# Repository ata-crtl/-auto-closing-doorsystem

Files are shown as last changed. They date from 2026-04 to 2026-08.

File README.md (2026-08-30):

# Automatic Door Closer

This is a rechargible door closer, it is designed to comabt the issue of people always leaveing my door open.You push the button once and there you go , the motor pulls in the fishing wire meaning you now have the ability to close the door from your bed. 

This system has a seprate remote and employs to esp32s to comunicate amongst each other and close the door from your bed. It is also desighned to be rechargible so you can maintain it.

## Features

- Rechargeable power system.
- ESP32 based control system.
- Separate remote Control
- Made to mount onto a door and above the door frame.

## Important Safety Check

Before attaching the wires to the ESP32 VIN pin, use a multimeter to make sure the wire coming from the buck converter is **5V** to not fry your esp and the same for the remote power output before connecting it to the ESP32.

## CAD

**Onshape link:**  
[View the Onshape model](https://cad.onshape.com/documents/bdd11de85f4570d51cb36bd7/w/b7536c01ad29c059d531be40/e/07df8b484f8b3f7ee84a2b9b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)

## Main Build Preview



## Bill of Materials

| Item | Notes | Link |
|---|---|---|
| ESP32 | Main controller for the door closer | https://www.aliexpress.com/item/1005008981904299.html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 |
| ESP32 | Controller used in the sender remote | https://www.aliexpress.com/item/1005008981904299.html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 |
| L298N motor driver | Drives the main motor | https://www.aliexpress.com/item/1005006794464360.html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 |
| High-power motor | Provides the force to close the door | https://www.aliexpress.com/item/1005008531655044.html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 |
| USB-C charging module | Charges the battery in the main unit | https://www.aliexpress.com/item/1005009041347980.html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 |
| TP4056 charging module | Charges the battery in the remote | https://www.aliexpress.com/item/1005012026232715.html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 |
| Buck converter | Steps voltage down to 5V for the ESP32 | https://www.aliexpress.com/item/1005011787585923.html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 |
| Boost/step-up module | Steps voltage up for the remote ESP32 | https://www.aliexpress.com/item/1005008964880397.html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 |
| Rechargeable battery | Main power source (12V) | https://www.aliexpress.com/item/32991156265.html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 |
| Rechargeable battery | Remote power source (3.7V) | https://www.aliexpress.com/item/1005008217717191.html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 |
| Push button | Used to trigger the system | https://www.aliexpress.com/item/1005007604615720.html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 |
| Fishing line | Connects the pulley system to the door | https://www.aliexpress.com/item/1005003972138352.html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 |
| Screws | Used to mount the mechanism and close the case (8mm) | https://www.aliexpress.com/item/1005003986879500.html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 |
| Screws | Used to mount the mechanism and close the case (20mm) | https://www.aliexpress.com/item/1005008669605569.html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 |
| Threaded inserts | Brass heat-set inserts for housing assembly | https://www.aliexpress.com/item/1005008897571758.html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 |
| Adhesive for wood | Used where needed for secure mounting | N/A |
| Multimeter | Needed to verify output voltage before wiring | N/A |
## Main Unit Connections

| Part | Pin | Connects to |
|---|-----|---|
| USB-C charging module | VO+ | Battery red (+) |
| USB-C charging module | VO- | Battery black (-) |
| Battery | Red (+) | Buck converter IN+ |
| Battery | Black (-) | Buck converter IN- |
| Battery | Black (-) | L298N GND terminal |
| Battery | Black (-) | USB-C module VO- |
| Buck converter | OUT+ | ESP32 VIN or 5V |
| Buck converter | OUT- | ESP32 GND |
| Battery | Red (+) | L298N 12V |
| Battery | Black (-) | L298N GND terminal |
| ESP32 | GPIO 12 | L298N IN1 |
| ESP32 | GPIO 13 | L298N IN2 |

Main unit wiring diagram

## Sender Remote Connections

| Part | Pin | Connects to |
|---|-----|---|
| Button | Leg 1 | ESP32 GPIO 15 |
| Button | Leg 2 | ESP32 GND |
| Battery | Positive | TP4056 B+ |
| Battery | Negative | TP4056 B- |
| TP4056 | OUT+ | Boost module VIN+ |
| TP4056 | OUT- | Boost module VIN- |
| Step-up module | VOUT+ | ESP32 5V |
| Step-up module | VOUT- | ESP32 GND |

## Electronics Overview

Electronics overview

## Assembly Instructions

### Main Mechanism

**Step 1:** Connect all the electronics.

**Step 2:** Connect these parts as shown below.

Assembly step 2

**Step 3:** Insert the assembly into the main frame as shown.

Assembly step 3

**Step 4:** Insert the part shown into the pulley system, then attach the motor.

Assembly step 4

**Step 5:** Insert the heated threaded inserts in the locations shown below.

Threaded inserts 1

Threaded inserts 2

Threaded inserts 3

Threaded inserts 4

Threaded inserts 5

**Step 6:** Secure the motor using the inserts as shown.

Motor secured

**Step 7:** Use three screws to secure the lid.

Assembly step 5

**Step 8:** Secure the unit to the door using four 20 mm screws.

Assembly step 6

**Step 9:** Attach the top mount above the door using four screws.

Assembly step 7

**Step 10:** Tie one end of the fishing line to the hole in the pulley wheel and the other end to the hook above the door.

Assembly step 8

### Remote

**Step 1:** Put the button through the hole in the lid.

Remote step 1

**Step 2:** Attach the electronics.

**Step 3:** Close the lid and screw it down using four screws.

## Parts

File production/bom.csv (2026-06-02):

Item | amount | Price (£) | Link
Nylon Monofilament Fishing Line 0.20mm | 1 | 0.75 | https://www.aliexpress.com/item/1005003972138352.html?curPageLogUid=2XcZ4Ww9MPOc
planetry gear motor 12v 222rpm shaft diameter8mm | 1 | 10.8 | https://www.aliexpress.com/item/1005008531655044.html?curPageLogUid=7DNxVExLPLAy
esp32 wroom | 2 | 8 | https://www.aliexpress.com/item/1005008981904299.html?curPageLogUid=QJ0YR3t2WHge
L298N | 1 | 1.93 | https://www.aliexpress.com/item/1005006794464360.html?curPageLogUid=icuTPAe6avr6
12V '1200mh lion battery | 1 | 6.19 | https://www.aliexpress.com/item/32991156265.html?curPageLogUid=CGYJoRuEcVPL
LM2596S step down | 1 | 0.61 | https://www.aliexpress.com/item/1005011787585923.html?curPageLogUid=YjcrZrW1Brqj
LION CHARGER | 1 | 2.12 | https://www.aliexpress.com/item/1005009041347980.html?curPageLogUid=TGs7hIvKGiPt
M2.5 * 8 screws | 11 | 2.88 | https://www.aliexpress.com/item/1005003986879500.html
metal button 16mm | 1 | 1.52 | https://www.aliexpress.com/item/1005007604615720.html?curPageLogUid=HykUMbSzUJwT
M2.5 * 20 screws | 8 | 1.90 | https://www.aliexpress.com/item/1005008669605569.html?curPageLogUid=YJ37Ofc631Vz
tp4056 | 1 | 0.33 | https://www.aliexpress.com/item/1005012026232715.html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
lipo battery 3.7v | 1 | 8.15 | https://www.aliexpress.com/item/1005008217717191.html?curPageLogUid=0eatIcatYKIL
XL6019 voltage boost unit | 1 | 1.72 | https://www.aliexpress.com/item/1005008964880397.html?curPageLogUid=0kPCptXNzxTl
3.5mmOD-m2.5mm threaded insterts | 18 | 2 | https://www.aliexpress.com/item/1005008897571758.html?curPageLogUid=Z5a6lezLlS6j
TOTAL |  | 49

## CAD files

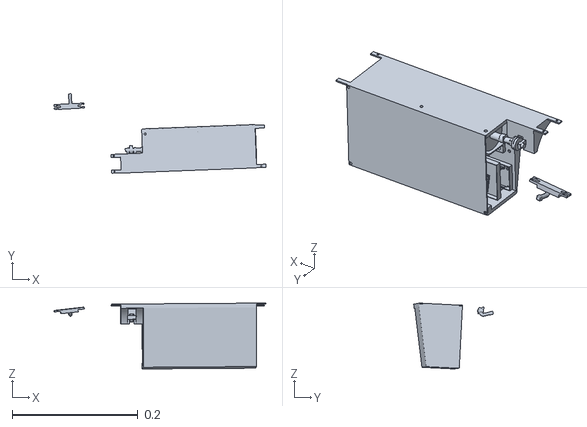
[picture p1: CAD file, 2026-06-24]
production/cad/Assembly 1 (2).stl
0.337 x 0.126 x 0.105

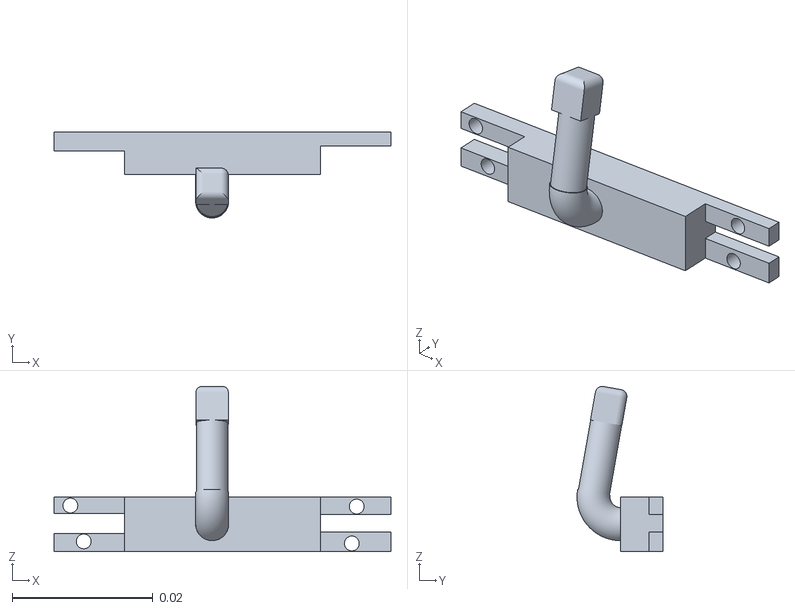
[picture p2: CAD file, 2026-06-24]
production/cad/Part Studio 3 (1).stl
0.0478 x 0.0122 x 0.0234

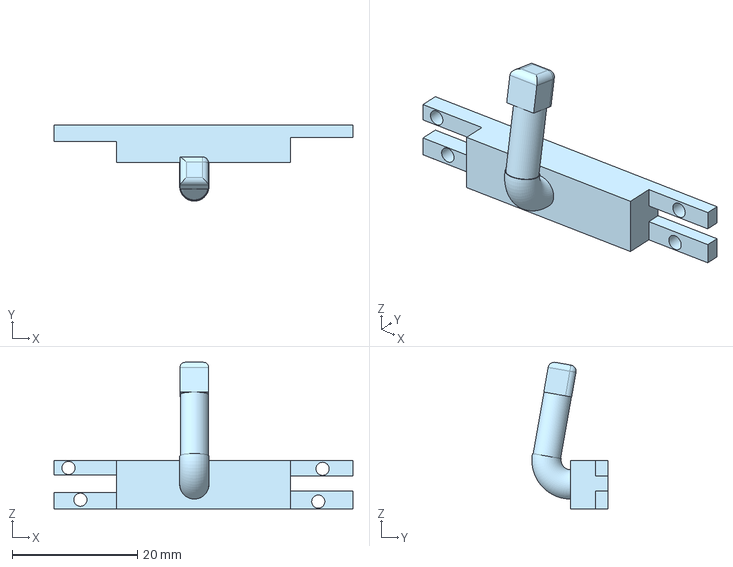
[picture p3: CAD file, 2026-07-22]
production/cad/stl cad files/Part Studio 3.step
47.8 x 12.2 x 23.4 mm

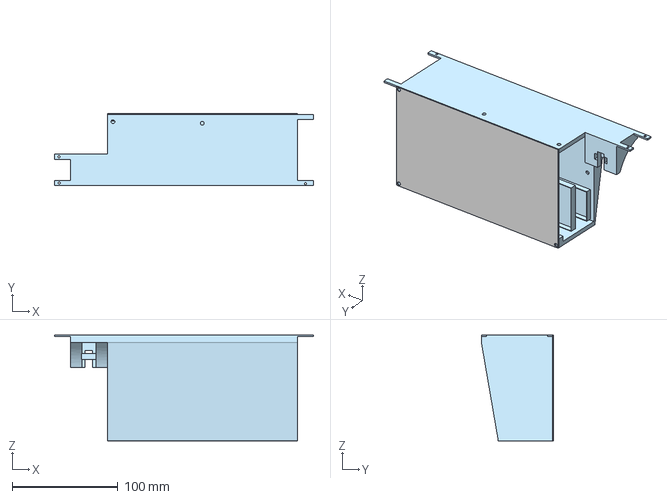
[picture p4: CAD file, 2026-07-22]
production/cad/stl cad files/frame.step
245.0 x 68.5 x 100.0 mm

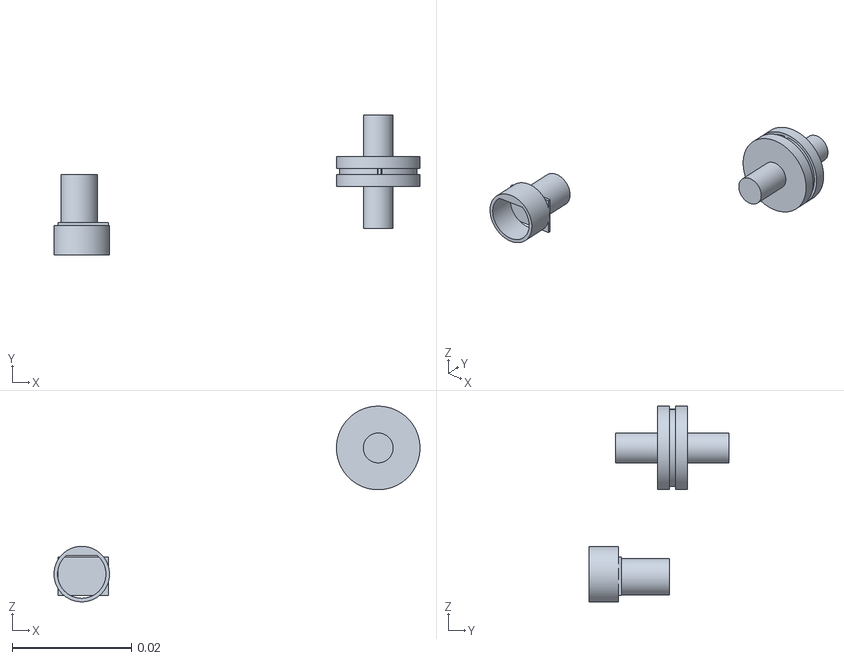
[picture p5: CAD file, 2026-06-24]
production/cad/Part Studio 2 (2).stl
0.0613 x 0.0235 x 0.0328

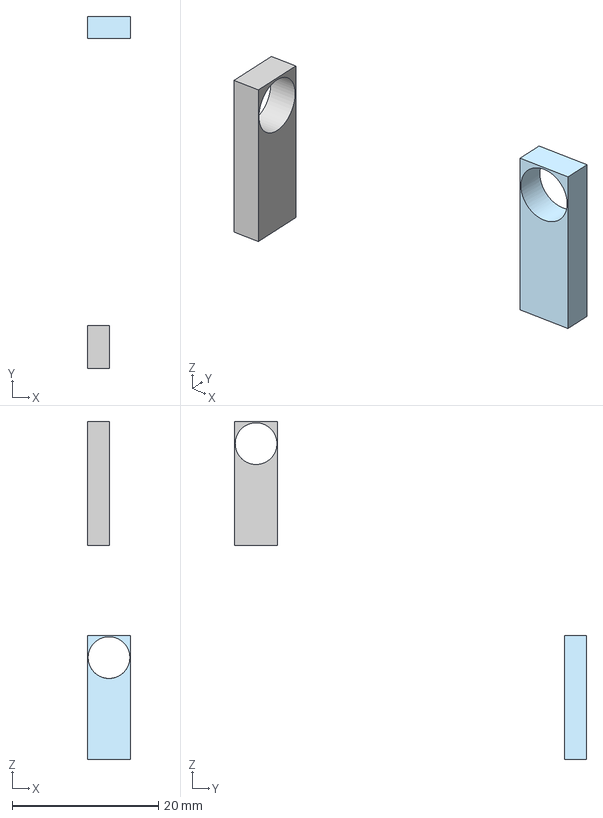
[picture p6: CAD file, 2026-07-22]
production/cad/stl cad files/Part Studio 4.step
5.90 x 48.1 x 46.2 mm

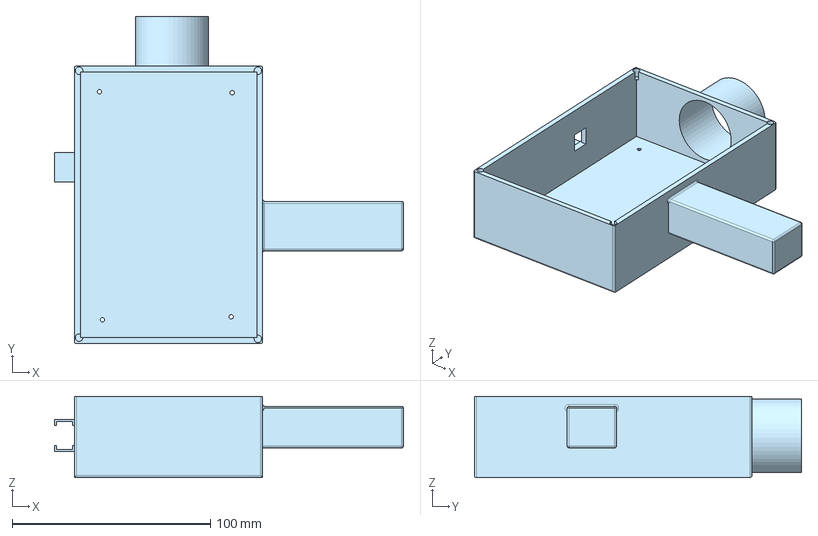
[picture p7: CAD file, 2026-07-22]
production/cad/stl cad files/Part Studio 1.step
176.0 x 165.0 x 41.0 mm

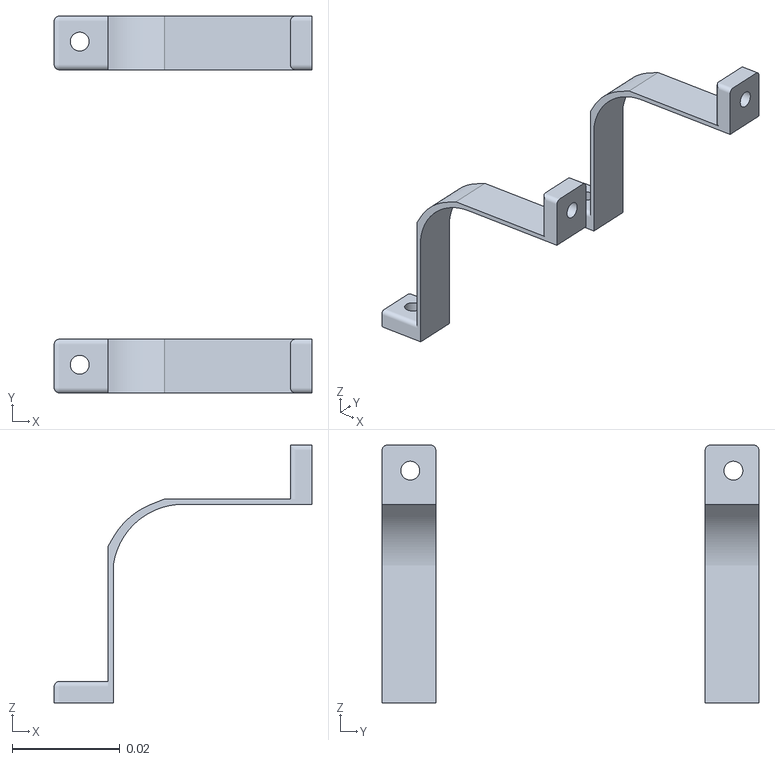
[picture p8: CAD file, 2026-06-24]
production/cad/holders motor.stl
0.0479 x 0.07 x 0.0479

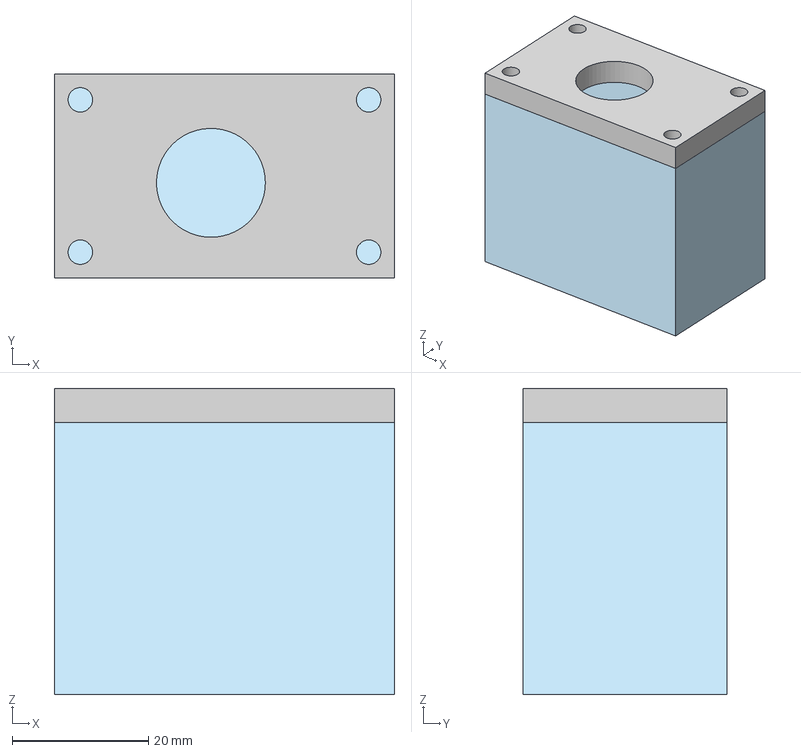
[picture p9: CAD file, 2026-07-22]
production/cad/stl cad files/remote.step
50.0 x 30.0 x 45.0 mm

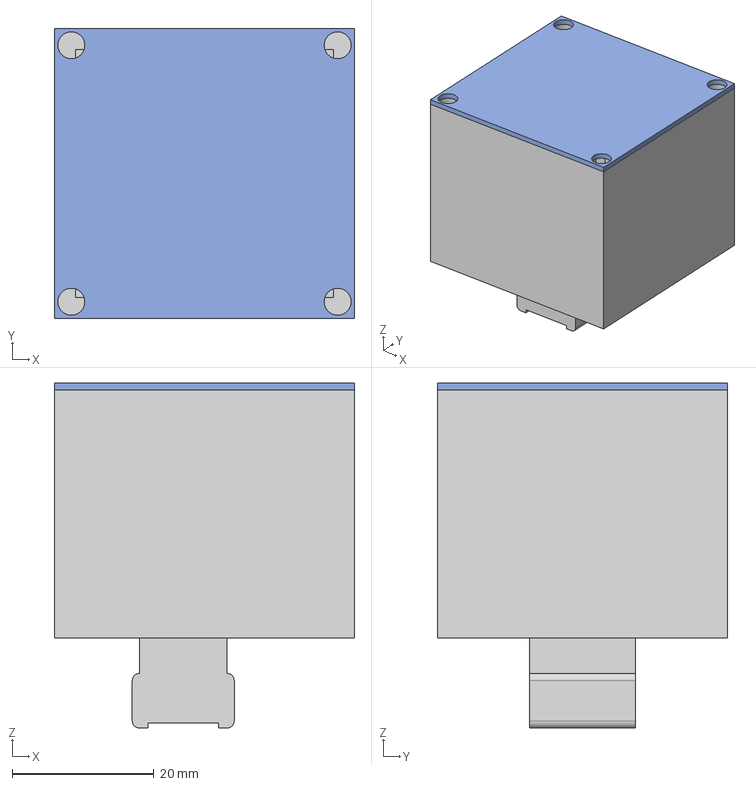
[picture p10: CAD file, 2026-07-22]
production/cad/stl cad files/Part Studio 2.step
42.4 x 41.0 x 48.7 mm

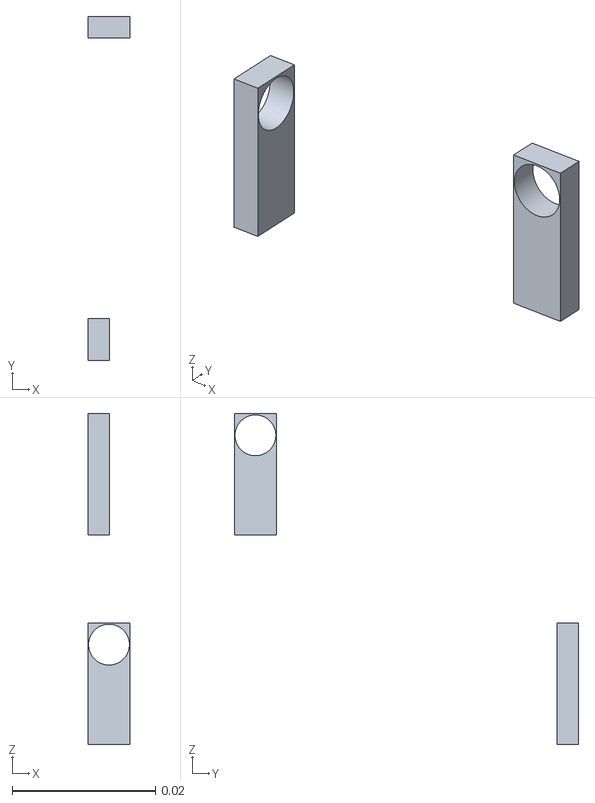
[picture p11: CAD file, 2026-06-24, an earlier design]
production/cad/Part Studio 4 (1).stl
0.0059 x 0.0481 x 0.0462

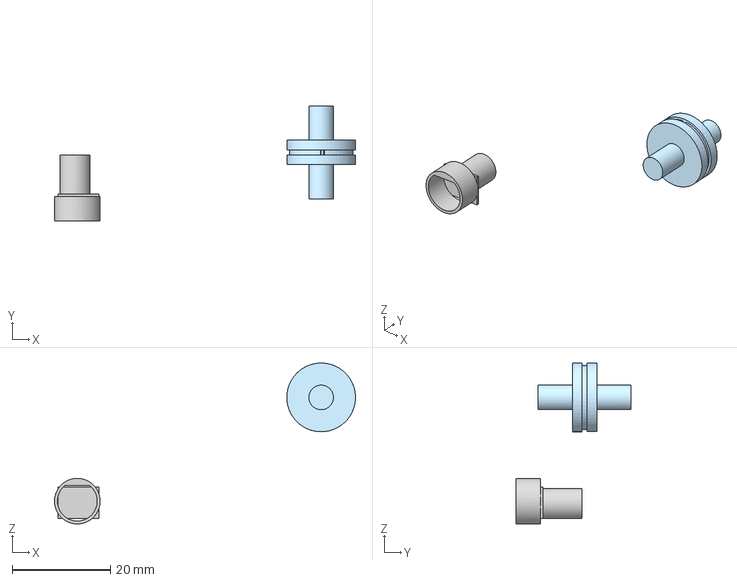
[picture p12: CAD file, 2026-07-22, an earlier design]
production/cad/stl cad files/Part Studio 2 (1).step
61.3 x 23.5 x 32.8 mm

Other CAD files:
production/cad/frame.stl
production/cad/remote.stl

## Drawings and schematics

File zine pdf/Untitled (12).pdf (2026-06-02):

## AUTO DOOR CLOSER

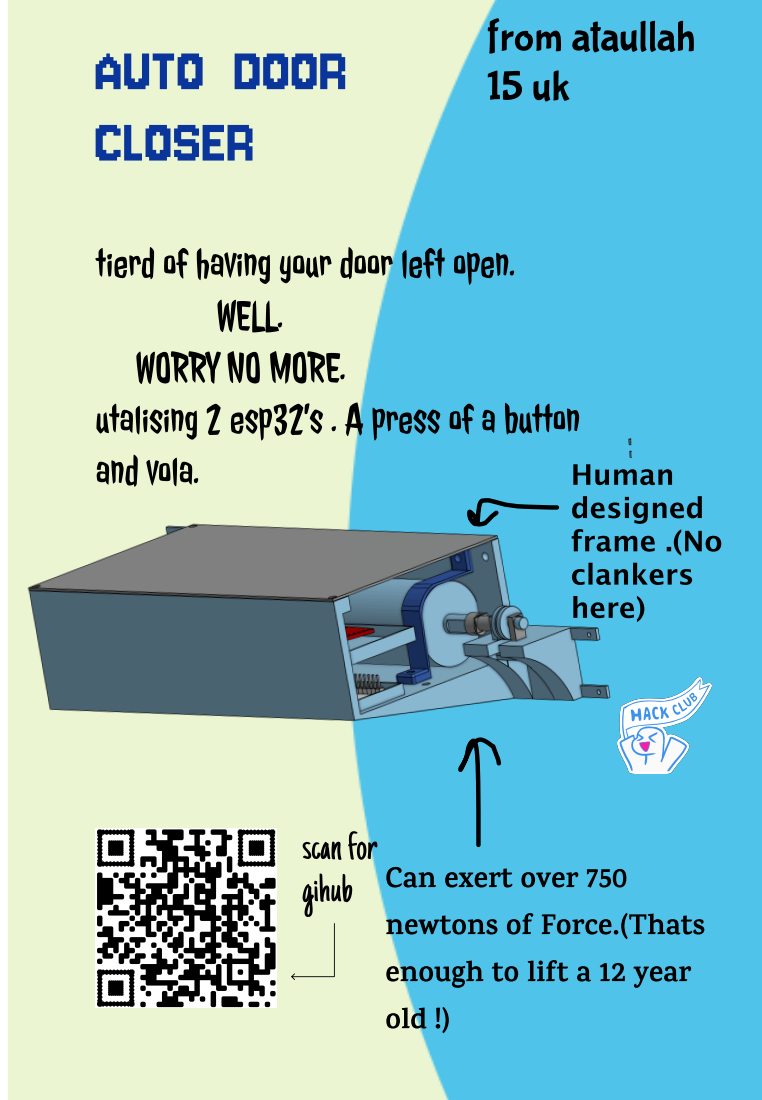
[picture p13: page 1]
from ataullah; and vola.; Human; designed frame .(No; clankers here); old !)

tierd of having your door left open.

WELL.
WORRY NO MORE.
utalising 2 esp32’s . A press of a button

scan for
gihub Can exert over 750

newtons of Force.(Thats

enough to lift a 12 year

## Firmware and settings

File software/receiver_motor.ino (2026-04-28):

// ============================================================
//  RECEIVER (Motor Controller Side)
//  Board: ESP32 Dev Module
//  Upload this to the ESP32 connected to the L298N.
// ============================================================

#include <esp_now.h>
#include <WiFi.h>

// --- PINS ----------------------------------------------------
const int IN1 = 12;   // PWM speed pin  → L298N IN1
const int IN2 = 13;   // Direction pin  → L298N IN2  (held LOW = forward)
// -------------------------------------------------------------

// --- SPEED TUNING --------------------------------------------
// Range: 0 (stopped) to 255 (full speed).
// Start at 100. If the motor hums but won't spin, raise to 130-160.
// If it's too fast, lower to 70-80.
int crawlSpeed = 100;
// -------------------------------------------------------------

// Motor state — toggled each time a command arrives
volatile bool motorActive = false;

// Message structure — must match sender exactly
typedef struct struct_message {
  bool toggleCmd;
} struct_message;

struct_message incomingData;   // Global buffer for received data

// *** FIX: parameter renamed to 'data' so it no longer shadows
//          the global 'incomingData' struct above.
//          (Original code had both named 'incomingData', causing
//           memcpy to corrupt the local pointer instead of filling
//           the global struct — resulting in a silent crash.)
void OnDataRecv(const uint8_t *mac, const uint8_t *data, int len) {
  memcpy(&incomingData, data, sizeof(incomingData));  // Safe copy into global

  motorActive = !motorActive;   // Flip the toggle

  Serial.print("Command received. Motor: ");
  Serial.println(motorActive ? "ON (Crawling)" : "OFF (Stopped)");
}

void setup() {
  Serial.begin(115200);

  // Motor pins
  pinMode(IN1, OUTPUT);
  pinMode(IN2, OUTPUT);

  // Make sure motor is stopped at boot
  digitalWrite(IN1, LOW);
  digitalWrite(IN2, LOW);

  WiFi.mode(WIFI_STA);

  if (esp_now_init() != ESP_OK) {
    Serial.println("ESP-NOW init failed — halting.");
    while (true) {}
  }

  esp_now_register_recv_cb(esp_now_recv_cb_t(OnDataRecv));

  Serial.println("Receiver ready. Waiting for toggle commands...");
}

void loop() {
  if (motorActive) {
    // --- FORWARD CRAWL (Method B: PWM on IN1, IN2 held LOW) ---
    // analogWrite works natively on ESP32 Arduino core 3.x+
    analogWrite(IN1, crawlSpeed);
    digitalWrite(IN2, LOW);
  } else {
    // --- STOP ---
    digitalWrite(IN1, LOW);
    digitalWrite(IN2, LOW);
  }

  delay(10);   // Small yield to keep the watchdog happy
}

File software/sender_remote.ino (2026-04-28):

// ============================================================
//  SENDER (Remote / Button Side)
//  Board: ESP32 Dev Module
//  Upload this to the ESP32 that has the button.
// ============================================================

#include <esp_now.h>
#include <WiFi.h>

// --- CONFIG --------------------------------------------------
const int BUTTON_PIN = 15;       // Button wired between GPIO 15 and GND
const unsigned long DEBOUNCE_MS = 50;
// -------------------------------------------------------------

// Broadcast to all nearby ESP32s (no pairing needed)
uint8_t broadcastAddress[] = {0xFF, 0xFF, 0xFF, 0xFF, 0xFF, 0xFF};

esp_now_peer_info_t peerInfo;

// Message structure — must match receiver exactly
typedef struct struct_message {
  bool toggleCmd;
} struct_message;

struct_message myData;

// Debounce state
int           lastButtonState   = HIGH;
unsigned long lastDebounceTime  = 0;

// Optional: called after each send so you can see if it worked
void OnDataSent(const uint8_t *mac_addr, esp_now_send_status_t status) {
  Serial.print("Send status: ");
  Serial.println(status == ESP_NOW_SEND_SUCCESS ? "OK" : "FAIL");
}

void setup() {
  Serial.begin(115200);

  // INPUT_PULLUP: pin floats HIGH, goes LOW when button pressed
  pinMode(BUTTON_PIN, INPUT_PULLUP);

  WiFi.mode(WIFI_STA);

  if (esp_now_init() != ESP_OK) {
    Serial.println("ESP-NOW init failed — halting.");
    while (true) {}   // Stop here so you see the error
  }

  esp_now_register_send_cb(OnDataSent);

  // Register broadcast peer
  memcpy(peerInfo.peer_addr, broadcastAddress, 6);
  peerInfo.channel = 0;
  peerInfo.encrypt = false;

  if (esp_now_add_peer(&peerInfo) != ESP_OK) {
    Serial.println("Failed to add peer — halting.");
    while (true) {}
  }

  Serial.println("Sender ready. Press button to toggle motor.");
}

void loop() {
  int reading = digitalRead(BUTTON_PIN);

  // Restart debounce timer whenever the reading changes
  if (reading != lastButtonState) {
    lastDebounceTime = millis();
  }

  // Only act once the reading has been stable for DEBOUNCE_MS
  if ((millis() - lastDebounceTime) > DEBOUNCE_MS) {
    if (reading == LOW) {                      // Button pressed
      myData.toggleCmd = true;
      esp_now_send(broadcastAddress, (uint8_t *)&myData, sizeof(myData));
      Serial.println("Toggle command sent.");

      // Wait for release so we only fire once per press
      while (digitalRead(BUTTON_PIN) == LOW) {
        delay(10);
      }
    }
  }

  lastButtonState = reading;
}

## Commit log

2026-04-22 Update and rename randok to BOM.csv
    [BOM.csv]
2026-05-03 Rename Assembly 1 (1).step to 3d model.step
    [3d model.step]
2026-05-14 Rename 3d model/Part Studio 3.step to hook.step
    [hook.step]
2026-05-14 Rename Part Studio 2.step to pulley wheel.step
    [pulley wheel.step]
2026-05-14 Rename Part Studio 4.step to pulley inserts.step
    [pulley inserts.step]
2026-05-14 Rename Part Studio 3.step to Anchor.step
    [Anchor.step]
